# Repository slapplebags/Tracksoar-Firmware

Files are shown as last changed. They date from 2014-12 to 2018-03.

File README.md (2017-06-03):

## Tracksoar Firmware
==========
This is a modified version of the [trackduino](https://github.com/trackuino/trackuino) firmware for the [Tracksoar](www.tracksoar.com) hardware.

### Configuring Hardware Version
This branch uses a super basic HAL and as a result must be told what version of hardware it is running on. [Edit the config here](https://github.com/slapplebags/Tracksoar-Firmware/blob/BME280-support/Tracksoar/Firmware/tracksoar/config.h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) to have the corect version uncommented. Everything before V1.2 should work as it normally did on the old set of sensors.

#### Build Status


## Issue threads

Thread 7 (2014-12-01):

Solar Version

slapplebags, 2014-12-01:
Create a solar version without 3.3 / 5v regs. Need to added a transistor to power up / down the radiometrix module and a buckboost to supply the 5v. Need to add a solar charger for lipo and see if the trackuino software will run at 4 or 8 mhz.

slapplebags, 2015-01-05:
By replacing the existing 5v regulator this could work with the existing design.

slapplebags, 2015-04-12:
Created solar version of the board.

Closed 2015-04-12.

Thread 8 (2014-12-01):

Update atmega328

slapplebags, 2014-12-01:
look into updating the atmega 328p to an atmega32u4 or similar for direct usb programability. This may shed some weight / size in connectors.

slapplebags, 2015-01-05:
Existing code allows for a atmega32u4, will looking into updating this on future revisions.

slapplebags, 2015-04-12:
Any future versions will be ARM based. Switching to the 32u4 is not worth the time to re-lay out the board . In addition a USB micro connector would not save space over the current FTDI connector.

Closed 2015-04-12.

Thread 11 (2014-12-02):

research new gps module

slapplebags, 2014-12-02:
look into the ublox uc530, it will fit on the existing board and integrates a chip antenna to reduce part count.

slapplebags, 2015-01-05:
Found the issue with the existing ublox max 7, need to provide power to the active antenna. However including the uc530 will reduce part count and weight by eliminating the u.fl connector and external active antenna. This will likely be included on the next revision.

slapplebags, 2015-04-12:
replaced max 7 with current gen max 8 / gps chip antenna and resolved issues with NMEA sentences. No need to move to the uc530.

Closed 2015-04-12.

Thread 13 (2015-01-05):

FTDI timeout

slapplebags, 2015-01-05:
When programming the board via FTDI the operation times out with no response. Seems to be related to the pull up / cap on the reset line.

slapplebags, 2015-01-05:
Reset cap was wired incorrectly on the board. Fixed by moving where cap is in the circuit. New boards have been ordered.

Closed 2015-01-05.

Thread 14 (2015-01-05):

Smaller GPS antenna

slapplebags, 2015-01-05:
Replace the existing GPS patch antenna with a smaller (fits within board outline) model. the following is a good candidate: http://www.taoglas.com/images/product_images/original_images/AP.10E.07.0039B.pdf

slapplebags, 2015-04-12:
Replaced with the above listed antenna, works well.

Closed 2015-04-12.

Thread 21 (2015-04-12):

No Sensor Data

slapplebags, 2015-04-12:
the current firmware does not include code for the BMP180 / SHT21 sensors.

slapplebags, 2015-04-27:
Latest commit to testing branch works! will make that the only firmware file shortly.

Closed 2015-04-27.

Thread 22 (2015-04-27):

Replace serial headers with MUX(S)

slapplebags, 2015-04-27:
Replace the painful and manual serial headers / jumpers with a mux to automatically select between programming and flight modes.

slapplebags, 2015-04-27:
reviewing using a pair of these muxes: http://www.ti.com/lit/ds/symlink/sn74lvc1g3157.pdf

slapplebags, 2015-05-18:
board has been created and ordered.

slapplebags, 2015-06-10:
test board arrived

slapplebags, 2015-07-31:
shelved for now, its a whole thing.

Closed 2015-07-31.

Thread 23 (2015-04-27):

Power Usage

slapplebags, 2015-04-27:
implement software power optimization. Batteries currently only 12 hours at room temp or last 3 hours at -40c.

mkapuscik, 2019-02-27:
So what in particular do you want optimized. Are there specific loops that are blocking that waste power? Sensors that stay on that shouldn't? Unnecessary delay calls?

It's incredibly helpful to characterize a problem before making an issue about it because it's much easier to tackle a specific set of symptoms that can be veritably solved than to "make it better" which could have no definite end and has infinite scope.

slapplebags, 2019-02-27:
Issue has been resolved, battery life extended to 36 hours at room temp and 12 hours at -40c.

Closed 2019-02-27.

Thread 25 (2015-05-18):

License

slapplebags, 2015-05-18:
update licenses to non-commercial until the board is ready for sale.

mkapuscik, 2016-09-05:
This is already the case for the hardware

Closed 2016-09-05.

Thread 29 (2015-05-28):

Integrate RF PA onto Tracksoar board.

mkapuscik, 2015-05-28:
Implement discrete component or monolithic RF PA onto Tracksoar PCB for 144MHz.

mkapuscik, 2015-05-28:
TI's CC11xx series monolithic transceivers have options that support 2-FSK modulation and the [CC1120](http://www.ti.com/lit/ds/symlink/cc1120.pdf) "supports" down to 136.7MHz however is not characterized below 169 MHz.

slapplebags, 2015-05-28:
what about the MAX2606, small package, low external part count, etc.

slapplebags, 2015-06-10:
also an ADL5545 to up the transmit power to 250mw

slapplebags, 2015-07-31:
Mike found a promising new chip, beat the info out of him so we can look into it.

slapplebags, 2015-09-14:
here's an example max2606: http://ram.lijun.li/old/various/fm_xmtr.html

slapplebags, 2016-02-01:
another possiblitity: http://digitalcommons.calpoly.edu/cgi/viewcontent.cgi?article=1156&context=eesp
also max2470 is a whole thing, use the micrl300

mkapuscik, 2019-02-27:
Wrong repo for this

Closed 2019-02-27.

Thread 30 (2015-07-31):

Sensor Calibration

slapplebags, 2015-07-31:
Running the tracksoar on the ground in stable conditions I get fairly poor data from the sensors, negative pressures at sea level, humidity off by 10%, and temp is questionable.

slapplebags, 2019-02-27:
BME280 sensor has resolved these issues.

Closed 2019-02-27.

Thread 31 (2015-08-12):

Potential Sensor Replacement

slapplebags, 2015-08-12:
replace the 2 sensors currently handling temperature / pressure / humidity with one sensor to handle all three such as:
http://www.mouser.com/ProductDetail/Bosch-Sensortec/BME280/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

mkapuscik, 2016-09-04:
See 5e0e7ec and let me know how testing works.

mkapuscik, 2016-09-05:
Test #39 with 1.2 and <1.2 boards and this can be resolved.

mkapuscik, 2019-02-27:
@slapplebags can you verify this is working. Can I close this?

slapplebags, 2019-02-27:
sensors have been replaced with the BME280 in tracksoar v1.2 and v2. Issue is resolved.

Closed 2019-02-27.

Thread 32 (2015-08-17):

GPS lost over 66426ft

slapplebags, 2015-08-17:
It looks like the GPS flight mode config at boot is happening correctly. May check the following: http://forum.arduino.cc/index.php?topic=232896.0
to resolve the issue and verify the config is happening.

slapplebags, 2015-09-10:
Verified that the GPS is being properly put into flight mode, the issue is the GPS antenna was getting too cold which detuned the antenna.

Closed 2015-09-10.

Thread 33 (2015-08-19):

add battery backup

slapplebags, 2015-08-19:
a battery like this would do nicely:
http://www.sii.co.jp/en/me/files/2014/11/BAC3011EJ-01C1409_web__.pdf

slapplebags, 2015-08-19:
added new board revision with a battery backup on board. Will send out for a new board revision soon.

Closed 2015-09-10.

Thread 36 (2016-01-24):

SD Card SRAM usage

slapplebags, 2016-01-24:
Look at switching to an eeprom like the ST Micro M24M02 to resolve issues with SD card library SRAM usage.

appropriate library for the ST Micro M24M02:
https://github.com/JChristensen/extEEPROM/blob/master/extEEPROM.cpp

slapplebags, 2019-02-27:
ATMega32u4 has enough SRAM to handle SD card / FAT libraries to enable onboard datalogging.

Closed 2019-02-27.

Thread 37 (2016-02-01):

Update Trackuino.ino to latest Arduino IDE

slapplebags, 2016-02-01:
The Trackuino.ide no longer compiles under 1.6.6+ due to a change in prog_uchar

slapplebags, 2016-02-01:
this may have point to a fix: http://arduino.stackexchange.com/questions/13816/updating-max7456-library-to-work-with-arduino-1-6-6

fake-name, 2018-03-24:
Works in current platformio.

slapplebags, 2019-02-27:
Issue is resolved. Tracksoar works with modern arduino versions.

Closed 2019-02-27.

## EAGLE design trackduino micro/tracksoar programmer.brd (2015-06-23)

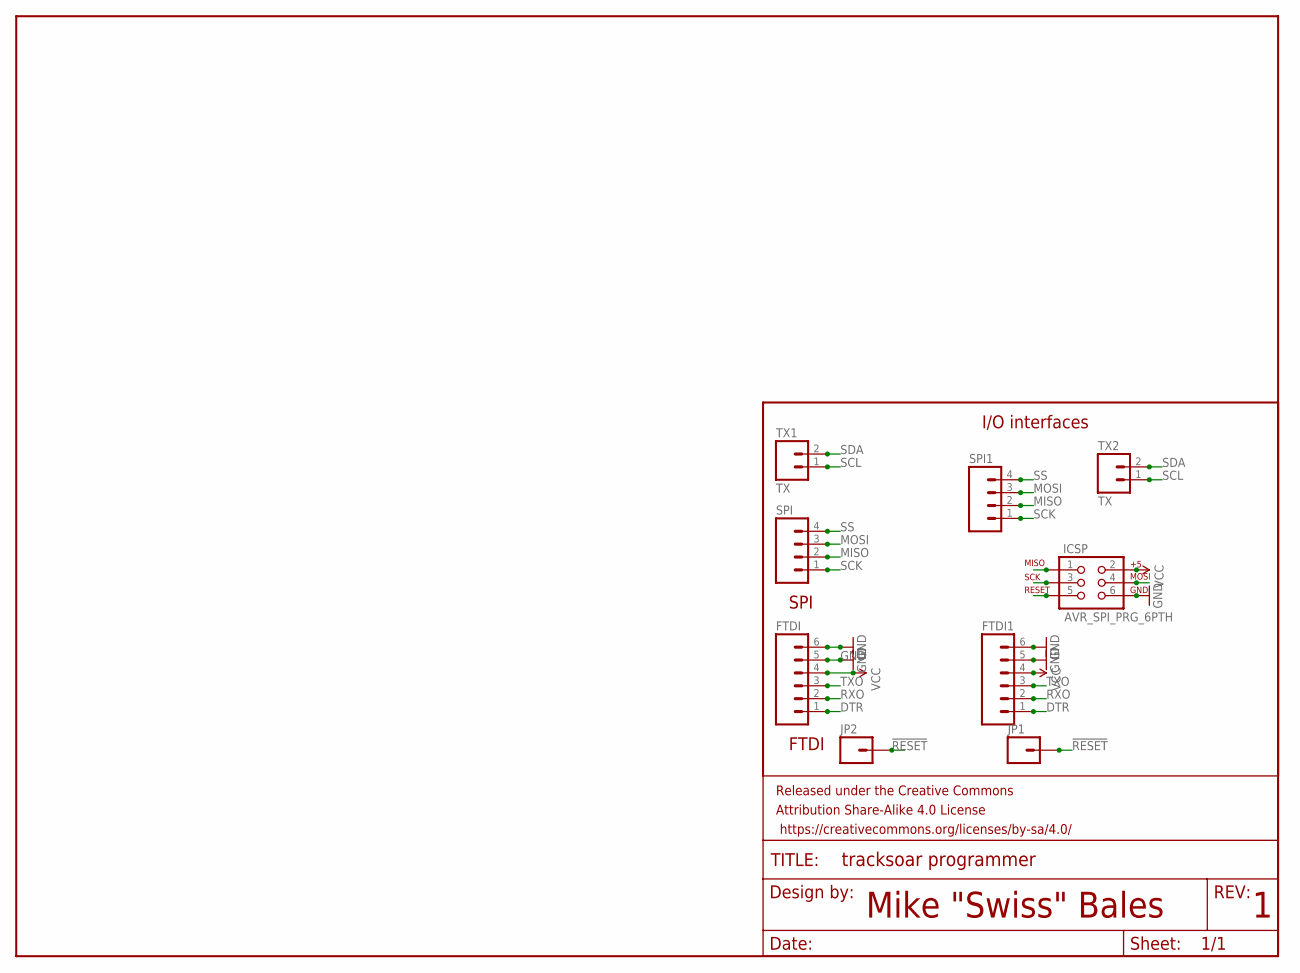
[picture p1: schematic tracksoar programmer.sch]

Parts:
FRAME1: FRAME-LETTER; CREATIVE_COMMONS
FTDI, FTDI1: M06NO_SILK_FEMALE_PTH; 1X06_NO_SILK
ICSP: AVR_SPI_PRG_6PTH; 2X3
JP1, JP2: M01PTH; 1X01
SPI, SPI1: M04JST-PTH-VERT; JST-4-PTH-VERT
TX1, TX2: TX; JST-2-PTH-VERT

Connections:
!RESET: ICSP.5, JP1.1, JP2.1
DTR: FTDI.1, FTDI1.1
GND: FTDI.5, FTDI.6, FTDI1.5, FTDI1.6, ICSP.6
MISO: ICSP.1, SPI.2, SPI1.2
MOSI: ICSP.4, SPI.3, SPI1.3
RXO: FTDI.2, FTDI1.2
SCK: ICSP.3, SPI.1, SPI1.1
SCL: TX1.1, TX2.1
SDA: TX1.2, TX2.2
SS: SPI.4, SPI1.4
TXO: FTDI.3, FTDI1.3
VCC: FTDI.4, FTDI1.4, ICSP.2

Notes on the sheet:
Mike "Swiss" Bales
I/O interfaces
SPI
FTDI

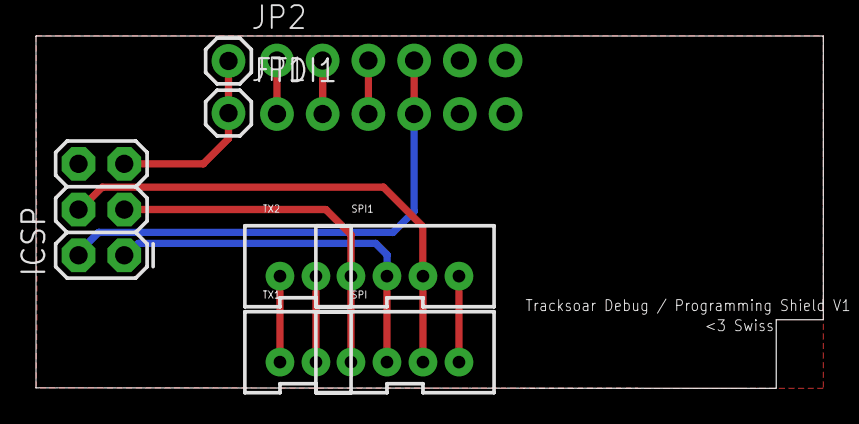
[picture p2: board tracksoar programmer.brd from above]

Board: 2 copper layers, 43.7 x 19.6 mm, 10 parts (1 on the bottom side), 12 nets.

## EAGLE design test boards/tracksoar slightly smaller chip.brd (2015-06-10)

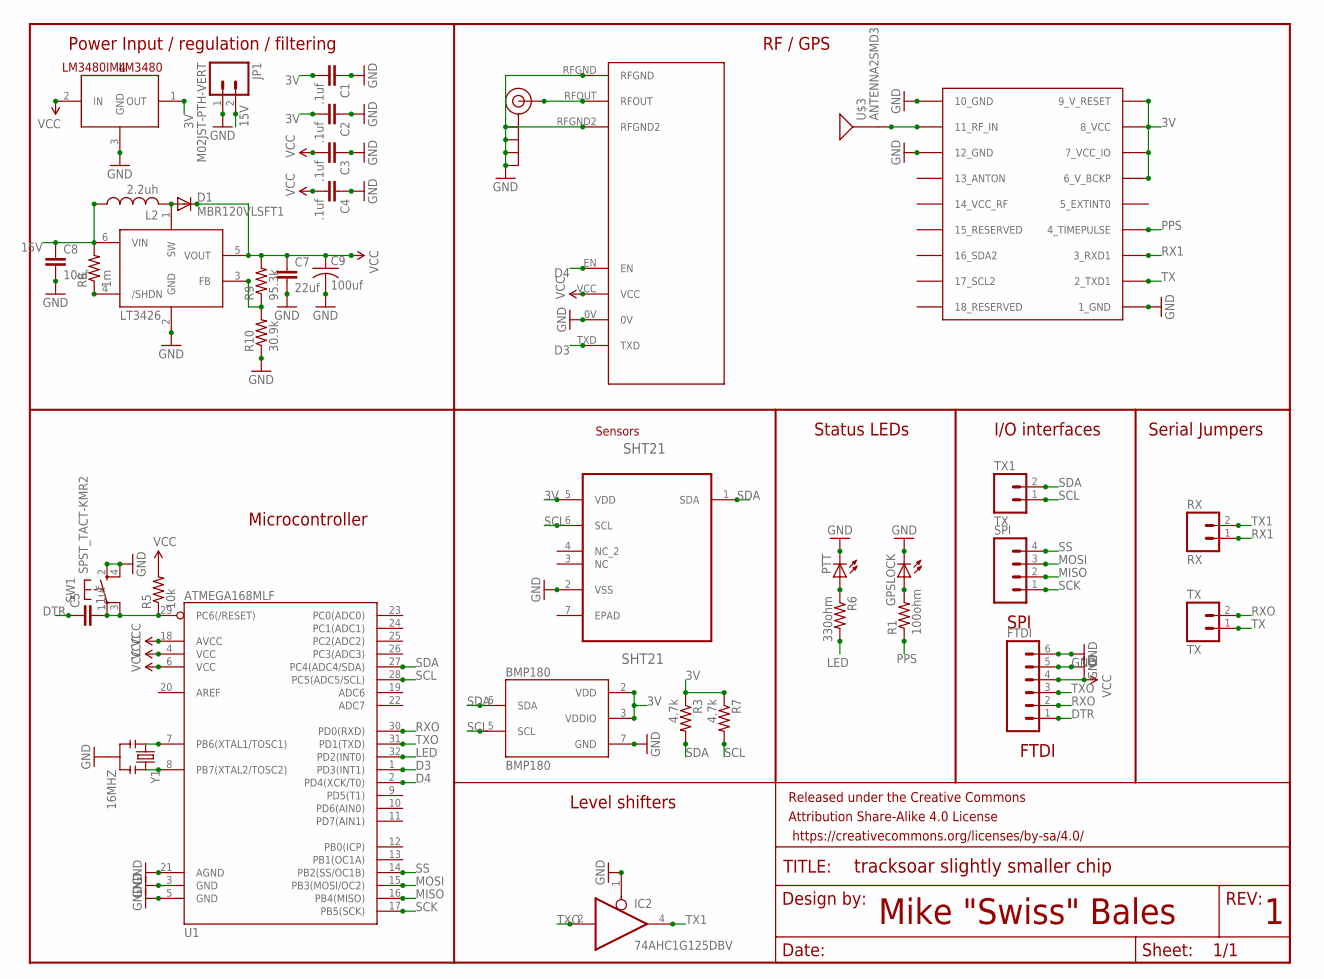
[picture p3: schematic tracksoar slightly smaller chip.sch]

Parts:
BMP180: BMP180
C1, C2, C3, C4, C5: .1uf; 0805
C7: 22uf; 0805
C8: 10uf; 0805
C9: 100uf; C1206
D1: MBR120VLSFT1; SOD123
FRAME1: FRAME-LETTER; CREATIVE_COMMONS
FTDI: M06NO_SILK_FEMALE_PTH; 1X06_NO_SILK
GPSLOCK: LEDCHIP-LED0805; CHIP-LED0805
IC2: 74AHC1G125DBV; SOT23-5
J$1: SMA_EDGE; SMA-EDGE
JP1: M02JST-PTH-VERT; JST-2-PTH-VERT
L2: 2.2uh; L1812
LM3480: LM3480IM4; SOT23-3
LT3426: LT3426; SOT23-6
PTT: LEDCHIP-LED0805; CHIP-LED0805
R1: 100ohm; 0805
R3, R7: 4.7k; 0805
R5: 10k; 0805
R6: 330ohm; 0805
R8: 1m; 0805
R9: 95.3k; 0805
R10: 30.9k; 0805
RX: RX; JST-2-PTH-VERT
SHT21: SHT21; DFN300X300X110-7N
SPI: M04JST-PTH-VERT; JST-4-PTH-VERT
SW1: SPST_TACT-KMR2; KMR2
TX, TX1: TX; JST-2-PTH-VERT
U1: ATMEGA168MLF; MLF32
U$1: UBLOX_MAX
U$2: RADIOMETRIX-HX1
U$3: ANTENNA2SMD3; ANTENNA-CHIP4
Y1: 16MHZ; RESONATOR-SMD

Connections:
3V: BMP180.2 (VDD), BMP180.3 (VDDIO), C1.2, C2.2, LM3480.1 (OUT), R3.1, R7.1, SHT21.5 (VDD), U$1.6_V_BCKP, U$1.7_VCC_IO, U$1.8_VCC, U$1.9_V_RESET
15V: C8.1, JP1.2, L2.1, LT3426.6 (VIN), R8.2
D3: U1.1 (PD3(INT1)), U$2.TXD
D4: U1.2 (PD4(XCK/T0)), U$2.EN
DTR: C5.1, FTDI.1
GND: BMP180.7 (GND), C1.1, C2.1, C3.1, C4.1, C7.2, C8.2, C9.2, FTDI.5, FTDI.6, GPSLOCK.C, IC2.1 (OE), IC2.3 (GND), J$1.GND@0 (GND), J$1.GND@1 (GND), J$1.GND@2 (GND), J$1.GND@3 (GND), JP1.1, LM3480.3 (GND), LT3426.2 (GND), PTT.C, R10.1, SHT21.2 (VSS), SW1.2 (S), SW1.4 (S1), U1.3 (GND), U1.5 (GND), U1.21 (AGND), U$1.1_GND, U$1.10_GND, U$1.12_GND, U$2.0V, U$2.RFGND, U$2.RFGND2, Y1.2
LED: R6.2, U1.32 (PD2(INT0))
MISO: SPI.2, U1.16 (PB4(MISO))
MOSI: SPI.3, U1.15 (PB3(MOSI/OC2))
unnamed: J$1.SIG (SIGNAL), U$2.RFOUT
unnamed: GPSLOCK.A, R1.2
unnamed: U$1.11_RF_IN, U$3.SIG
unnamed: D1.A, L2.2, LT3426.1 (SW)
unnamed: LT3426.4 (/SHDN), R8.1
unnamed: LT3426.3 (FB), R9.1, R10.2
unnamed: U1.8 (PB7(XTAL2/TOSC2)), Y1.3
unnamed: C5.2, R5.1, SW1.1, SW1.3 (P1), U1.29 (PC6(/RESET))
unnamed: U1.7 (PB6(XTAL1/TOSC1)), Y1.1
unnamed: PTT.A, R6.1
PPS: R1.1, U$1.4_TIMEPULSE
RX1: RX.1, U$1.3_RXD1
RXO: FTDI.2, TX.2, U1.30 (PD0(RXD))
SCK: SPI.1, U1.17 (PB5(SCK))
SCL: BMP180.5 (SCL), R7.2, SHT21.6 (SCL), TX1.1, U1.28 (PC5(ADC5/SCL))
SDA: BMP180.6 (SDA), R3.2, SHT21.1 (SDA), TX1.2, U1.27 (PC4(ADC4/SDA))
SS: SPI.4, U1.14 (PB2(SS/OC1B))
TX: TX.1, U$1.2_TXD1
TX1: IC2.4 (O), RX.2
TXO: FTDI.3, IC2.2 (I), U1.31 (PD1(TXD))
VCC: C3.2, C4.2, C7.1, C9.1, D1.C, FTDI.4, IC2.5 (VCC), LM3480.2 (IN), LT3426.5 (VOUT), R5.2, R9.2, U1.4 (VCC), U1.6 (VCC), U1.18 (AVCC), U$2.VCC

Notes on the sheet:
Mike "Swiss" Bales
Power Input / regulation / filtering
RF / GPS
Microcontroller
Level shifters
Status LEDs
I/O interfaces
Serial Jumpers
SPI
FTDI
Sensors

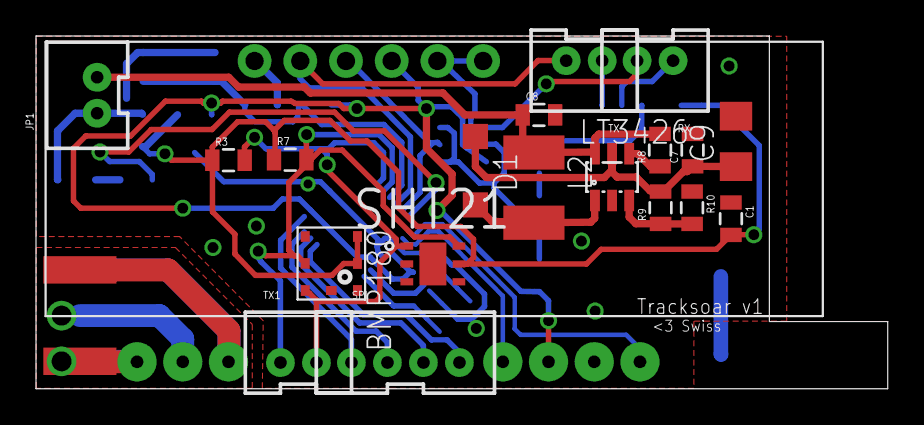
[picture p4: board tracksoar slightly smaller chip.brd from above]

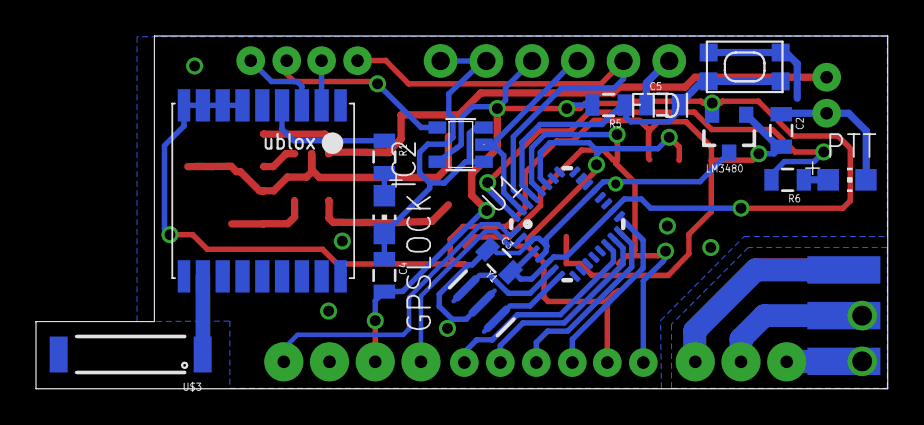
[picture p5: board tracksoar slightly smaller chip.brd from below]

Board: 2 copper layers, 47.3 x 19.6 mm, 39 parts (18 on the bottom side), 30 nets.

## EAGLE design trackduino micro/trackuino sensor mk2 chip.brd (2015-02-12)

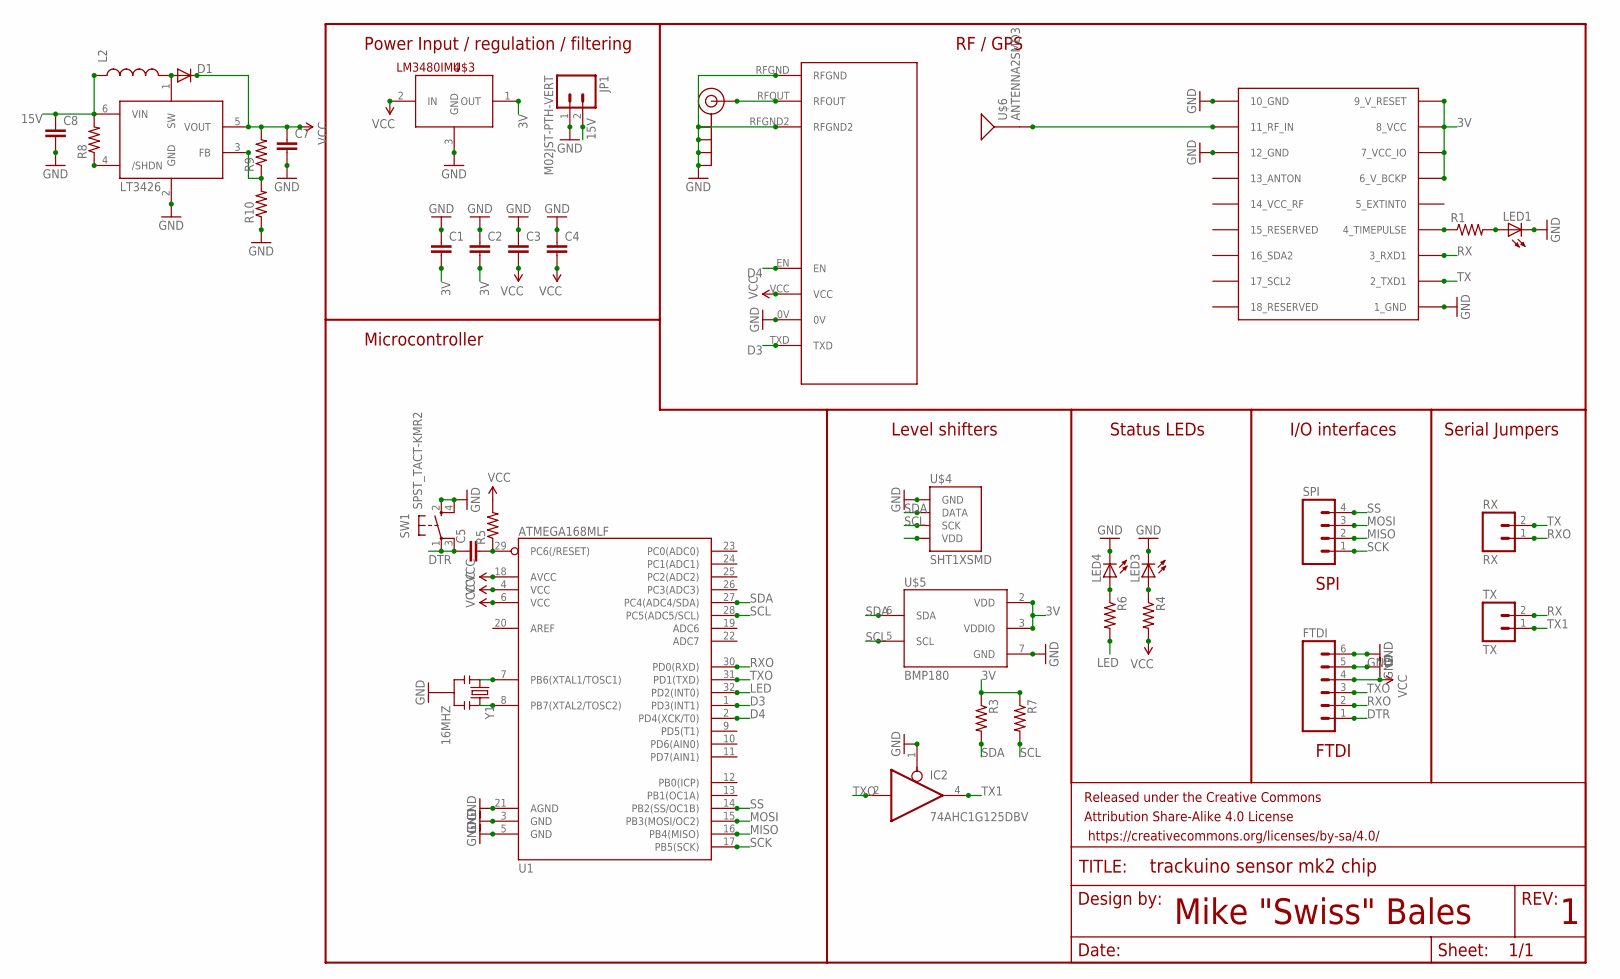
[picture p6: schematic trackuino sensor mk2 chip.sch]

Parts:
C1, C2, C3, C4, C5, C7, C8: CAP0805; 0805
D1: DIODE-SOD123; SOD123
FRAME1: FRAME-LETTER; CREATIVE_COMMONS
FTDI: M06NO_SILK_FEMALE_PTH; 1X06_NO_SILK
IC2: 74AHC1G125DBV; SOT23-5
J$1: SMA_EDGE; SMA-EDGE
JP1: M02JST-PTH-VERT; JST-2-PTH-VERT
L2: INDUCTOR0805; 0805
LED1, LED3, LED4: LEDCHIP-LED0805; CHIP-LED0805
R1, R3, R4, R5, R6, R7, R8, R9, R10: RESISTOR0805-RES; 0805
RX: RX; 1X02
SPI: M041X04_NO_SILK; 1X04_NO_SILK
SW1: SPST_TACT-KMR2; KMR2
TX: TX; 1X02
U1: ATMEGA168MLF; MLF32
U$1: UBLOX_MAX
U$2: RADIOMETRIX-HX1
U$3: LM3480IM4; SOT23-3
U$4: SHT1XSMD; SHT1X
U$5: BMP180
U$6: ANTENNA2SMD3; ANTENNA-CHIP4
U$7: LT3426; SOT23-6
Y1: 16MHZ; RESONATOR-SMD

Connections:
3V: C1.2, C2.2, R3.1, R7.1, U$1.6_V_BCKP, U$1.7_VCC_IO, U$1.8_VCC, U$1.9_V_RESET, U$3.1 (OUT), U$4.4 (VDD), U$5.2 (VDD), U$5.3 (VDDIO)
15V: C8.1, JP1.2, L2.1, R8.2, U$7.6 (VIN)
D3: U1.1 (PD3(INT1)), U$2.TXD
D4: U1.2 (PD4(XCK/T0)), U$2.EN
DTR: C5.1, FTDI.1, SW1.1, SW1.3 (P1)
GND: C1.1, C2.1, C3.1, C4.1, C7.2, C8.2, FTDI.5, FTDI.6, IC2.1 (OE), IC2.3 (GND), J$1.GND@0 (GND), J$1.GND@1 (GND), J$1.GND@2 (GND), J$1.GND@3 (GND), JP1.1, LED1.C, LED3.C, LED4.C, R10.1, SW1.2 (S), SW1.4 (S1), U1.3 (GND), U1.5 (GND), U1.21 (AGND), U$1.1_GND, U$1.10_GND, U$1.12_GND, U$2.0V, U$2.RFGND, U$2.RFGND2, U$3.3 (GND), U$4.1 (GND), U$5.7 (GND), U$7.2 (GND), Y1.2
LED: R6.2, U1.32 (PD2(INT0))
MISO: SPI.2, U1.16 (PB4(MISO))
MOSI: SPI.3, U1.15 (PB3(MOSI/OC2))
unnamed: J$1.SIG (SIGNAL), U$2.RFOUT
unnamed: R1.1, U$1.4_TIMEPULSE
unnamed: LED1.A, R1.2
unnamed: U$1.11_RF_IN, U$6.SIG
unnamed: C5.2, R5.1, U1.29 (PC6(/RESET))
unnamed: LED3.A, R4.1
unnamed: D1.A, L2.2, U$7.1 (SW)
unnamed: R8.1, U$7.4 (/SHDN)
unnamed: R9.1, R10.2, U$7.3 (FB)
unnamed: U1.8 (PB7(XTAL2/TOSC2)), Y1.3
unnamed: U1.7 (PB6(XTAL1/TOSC1)), Y1.1
unnamed: LED4.A, R6.1
RX: TX.2, U$1.3_RXD1
RXO: FTDI.2, RX.1, U1.30 (PD0(RXD))
SCK: SPI.1, U1.17 (PB5(SCK))
SCL: R7.2, U1.28 (PC5(ADC5/SCL)), U$4.3 (SCK), U$5.5 (SCL)
SDA: R3.2, U1.27 (PC4(ADC4/SDA)), U$4.2 (DATA), U$5.6 (SDA)
SS: SPI.4, U1.14 (PB2(SS/OC1B))
TX: RX.2, U$1.2_TXD1
TX1: IC2.4 (O), TX.1
TXO: FTDI.3, IC2.2 (I), U1.31 (PD1(TXD))
VCC: C3.2, C4.2, C7.1, D1.C, FTDI.4, IC2.5 (VCC), R4.2, R5.2, R9.2, U1.4 (VCC), U1.6 (VCC), U1.18 (AVCC), U$2.VCC, U$3.2 (IN), U$7.5 (VOUT)

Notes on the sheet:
Mike "Swiss" Bales
Power Input / regulation / filtering
RF / GPS
Microcontroller
Level shifters
Status LEDs
I/O interfaces
Serial Jumpers
SPI
FTDI

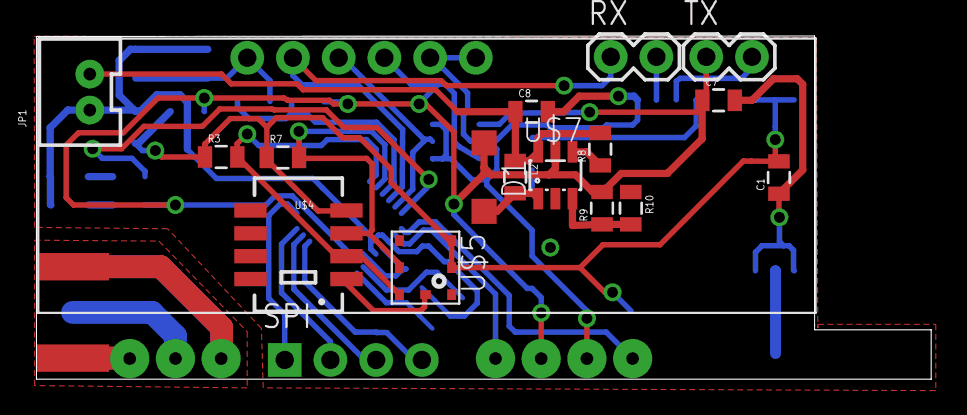
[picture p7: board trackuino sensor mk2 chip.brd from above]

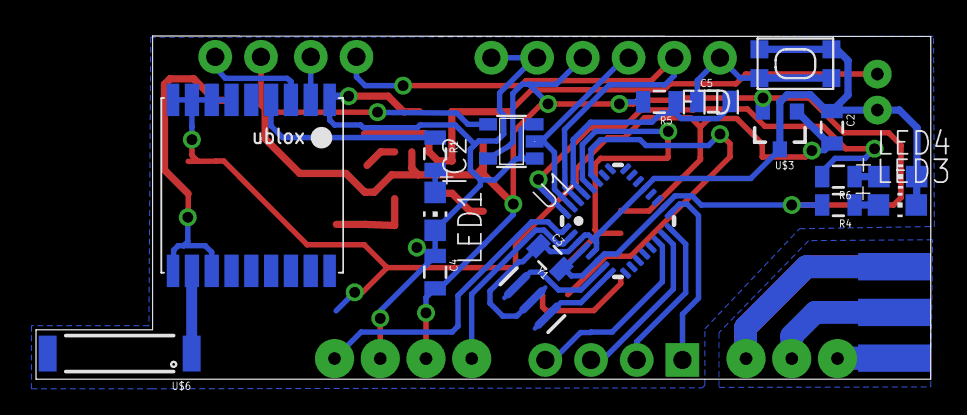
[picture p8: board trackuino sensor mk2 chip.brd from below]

Board: 2 copper layers, 49.7 x 19.1 mm, 39 parts (20 on the bottom side), 31 nets.

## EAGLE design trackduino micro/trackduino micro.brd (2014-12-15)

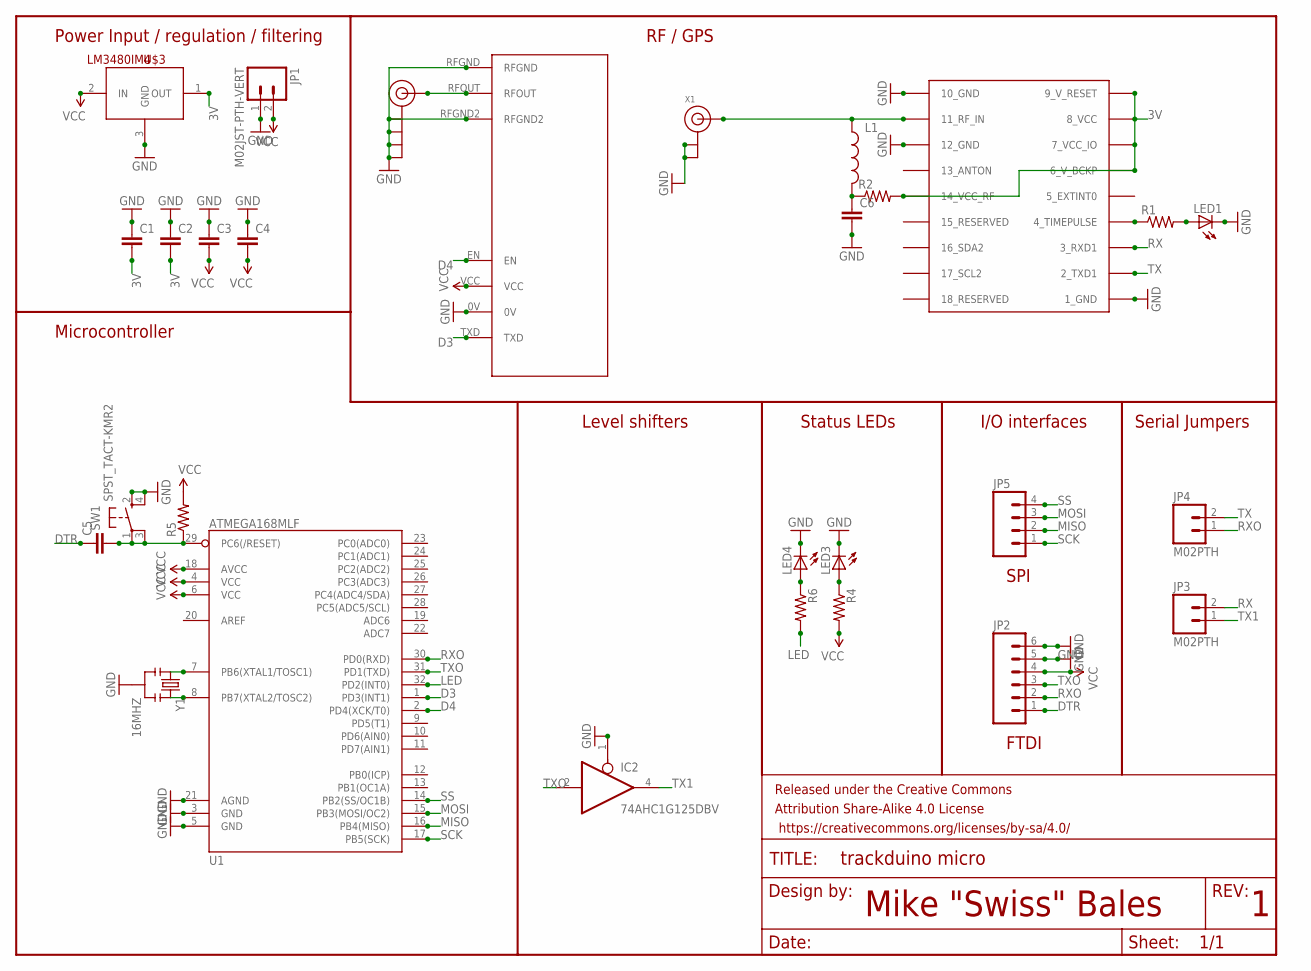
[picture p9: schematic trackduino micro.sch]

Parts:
C1, C2, C3, C4, C5, C6: CAP0805; 0805
FRAME1: FRAME-LETTER; CREATIVE_COMMONS
IC2: 74AHC1G125DBV; SOT23-5
J$1: SMA_EDGE; SMA-EDGE
JP1: M02JST-PTH-VERT; JST-2-PTH-VERT
JP2: M06NO_SILK_FEMALE_PTH; 1X06_NO_SILK
JP3, JP4: M02PTH; 1X02
JP5: M041X04_NO_SILK; 1X04_NO_SILK
L1: INDUCTOR0805; 0805
LED1, LED3, LED4: LEDCHIP-LED0805; CHIP-LED0805
R1, R2, R4, R5, R6: RESISTOR0805-RES; 0805
SW1: SPST_TACT-KMR2; KMR2
U1: ATMEGA168MLF; MLF32
U$1: UBLOX_MAX
U$2: RADIOMETRIX-HX1
U$3: LM3480IM4; SOT23-3
X1: ANTENNA_U.FL; U.FL
Y1: 16MHZ; RESONATOR-SMD

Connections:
3V: C1.2, C2.2, R2.2, U$1.6_V_BCKP, U$1.7_VCC_IO, U$1.8_VCC, U$1.9_V_RESET, U$1.14_VCC_RF, U$3.1 (OUT)
D3: U1.1 (PD3(INT1)), U$2.TXD
D4: U1.2 (PD4(XCK/T0)), U$2.EN
DTR: C5.1, JP2.1
GND: C1.1, C2.1, C3.1, C4.1, C6.2, IC2.1 (OE), IC2.3 (GND), J$1.GND@0 (GND), J$1.GND@1 (GND), J$1.GND@2 (GND), J$1.GND@3 (GND), JP1.1, JP2.5, JP2.6, LED1.C, LED3.C, LED4.C, SW1.2 (S), SW1.4 (S1), U1.3 (GND), U1.5 (GND), U1.21 (AGND), U$1.1_GND, U$1.10_GND, U$1.12_GND, U$2.0V, U$2.RFGND, U$2.RFGND2, U$3.3 (GND), X1.1 (GND), X1.2 (GND), Y1.2
LED: R6.2, U1.32 (PD2(INT0))
MISO: JP5.2, U1.16 (PB4(MISO))
MOSI: JP5.3, U1.15 (PB3(MOSI/OC2))
unnamed: J$1.SIG (SIGNAL), U$2.RFOUT
unnamed: R1.1, U$1.4_TIMEPULSE
unnamed: LED1.A, R1.2
unnamed: L1.1, U$1.11_RF_IN, X1.3 (SIGNAL)
unnamed: LED3.A, R4.1
unnamed: C5.2, R5.1, SW1.1, SW1.3 (P1), U1.29 (PC6(/RESET))
unnamed: U1.8 (PB7(XTAL2/TOSC2)), Y1.3
unnamed: C6.1, L1.2, R2.1
unnamed: U1.7 (PB6(XTAL1/TOSC1)), Y1.1
unnamed: LED4.A, R6.1
RX: JP3.2, U$1.3_RXD1
RXO: JP2.2, JP4.1, U1.30 (PD0(RXD))
SCK: JP5.1, U1.17 (PB5(SCK))
SS: JP5.4, U1.14 (PB2(SS/OC1B))
TX: JP4.2, U$1.2_TXD1
TX1: IC2.4 (O), JP3.1
TXO: IC2.2 (I), JP2.3, U1.31 (PD1(TXD))
VCC: C3.2, C4.2, IC2.5 (VCC), JP1.2, JP2.4, R4.2, R5.2, U1.4 (VCC), U1.6 (VCC), U1.18 (AVCC), U$2.VCC, U$3.2 (IN)

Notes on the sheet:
Mike "Swiss" Bales
Power Input / regulation / filtering
RF / GPS
Microcontroller
Level shifters
Status LEDs
I/O interfaces
Serial Jumpers
SPI
FTDI

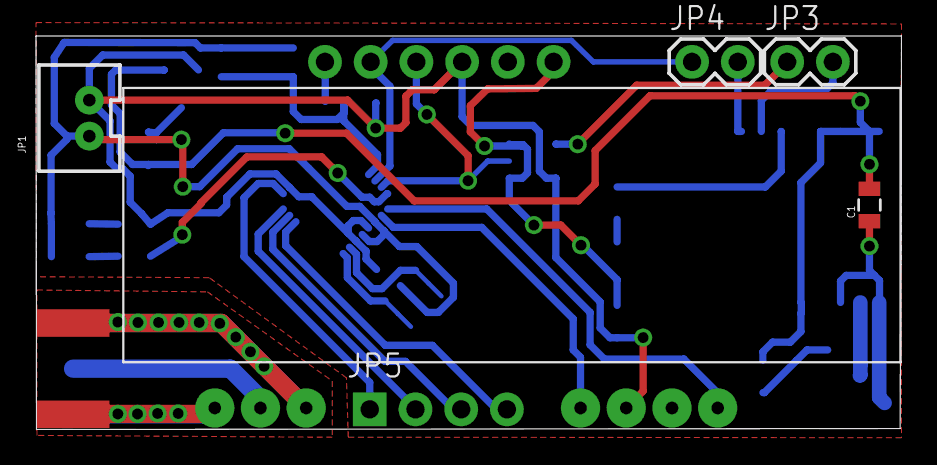
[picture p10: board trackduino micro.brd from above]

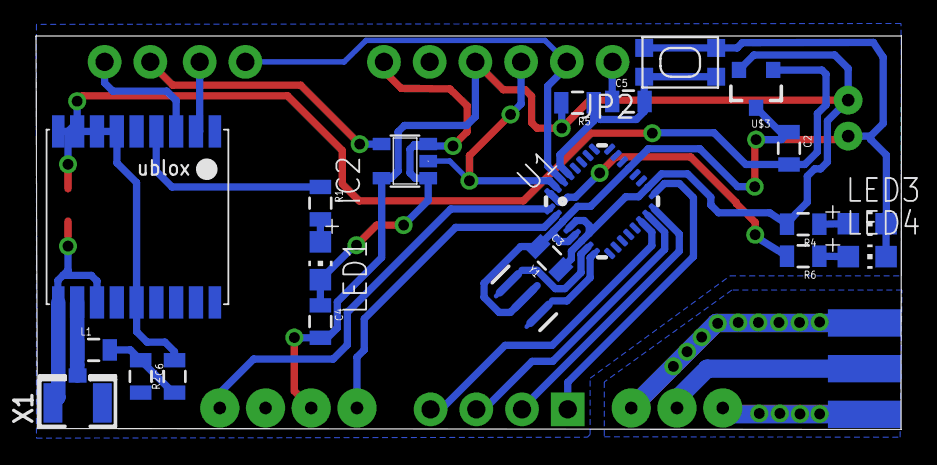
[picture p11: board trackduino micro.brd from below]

Board: 2 copper layers, 48.1 x 21.9 mm, 30 parts (23 on the bottom side), 26 nets.

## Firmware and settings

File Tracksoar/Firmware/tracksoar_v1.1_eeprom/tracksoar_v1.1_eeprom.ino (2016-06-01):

/* trackuino copyright (C) 2010  EA5HAV Javi
 *
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
 * You should have received a copy of the GNU General Public License
 * along with this program; if not, write to the Free Software
 * Foundation, Inc., 51 Franklin Street, Fifth Floor, Boston, MA  02110-1301, USA.
 */

// Mpide 22 fails to compile Arduino code because it stupidly defines ARDUINO 
// as an empty macro (hence the +0 hack). UNO32 builds are fine. Just use the
// real Arduino IDE for Arduino builds. Optionally complain to the Mpide
// authors to fix the broken macro.
#if (ARDUINO + 0) == 0
#error "Oops! We need the real Arduino IDE (version 22 or 23) for Arduino builds."
#error "See trackuino.pde for details on this"

// Refuse to compile on arduino version 21 or lower. 22 includes an
// optimization of the USART code that is critical for real-time operation
// of the AVR code.
#elif (ARDUINO + 0) < 22
#error "Oops! We need Arduino 22 or 23"
#error "See trackuino.pde for details on this"

#endif


// Trackuino custom libs
#include "config.h"
#include "afsk_avr.h"
//#include "afsk_pic32.h"
#include "aprs.h"
//#include "buzzer.h"
#include "gps.h"
#include "pin.h"
#include "power.h"
#include "sensors_avr.h"
//#include "sensors_pic32.h"
//#include <SPI.h>
//#include <SD.h>

// Arduino/AVR libs
#if (ARDUINO + 1) >= 100
#  include <Arduino.h>
#else
#  include <WProgram.h>
#endif
#define cbi(sfr, bit) (_SFR_BYTE(sfr) &= ~_BV(bit))
// Module constants
static const uint32_t VALID_POS_TIMEOUT = 2000;  // ms

// Though not used here, we need to include Wire.h in this file for other code:
#include <Wire.h>

#include "extEEPROM.h"

// Module variables
static int32_t next_aprs = 0;
uint32_t g_last_data_write_time = 0;
extEEPROM g_EEPROM(kbits_2048, 1, 256);

void setup()
{
  pinMode(LED_PIN, OUTPUT);
  pin_write(LED_PIN, LOW);

// deactivate internal pull-ups for twi
    // as per note from atmega8 manual pg167
    cbi(PORTC, 4);
    cbi(PORTC, 5);

  Serial.begin(GPS_BAUDRATE);
#ifdef DEBUG_RESET
  Serial.println("RESET");
#endif

//  buzzer_setup();
  afsk_setup();
  gps_setup();
  sensors_setup();

#ifdef DEBUG_SENS
  Serial.print("Ti=");
  Serial.print(sensors_int_lm60());
  Serial.print(", Te=");
  Serial.print(sensors_ext_lm60());
  Serial.print(", Vin=");
  Serial.println(sensors_vin());
#endif

  // Do not start until we get a valid time reference
  // for slotted transmissions.
  if (APRS_SLOT >= 0) {
    do {
      while (! Serial.available())
        power_save();
    } while (! gps_decode(Serial.read()));
    
    next_aprs = millis() + 1000 *
      (APRS_PERIOD - (gps_seconds + APRS_PERIOD - APRS_SLOT) % APRS_PERIOD);
  }
  else {
    next_aprs = millis();
  }  
  // TODO: beep while we get a fix, maybe indicating the number of
  // visible satellites by a series of short beeps?
}

void get_pos()
{
  // Get a valid position from the GPS
  int valid_pos = 0;
  uint32_t timeout = millis();
  do {
    if (Serial.available())
      valid_pos = gps_decode(Serial.read());
  } while ( (millis() - timeout < VALID_POS_TIMEOUT) && ! valid_pos) ;

}

void writeData()
{
  g_EEPROM.writeData(gps_time);
  g_EEPROM.writeData(gps_seconds);
  g_EEPROM.writeData(gps_lat);
  g_EEPROM.writeData(gps_lon);
  g_EEPROM.writeData(gps_altitude);
  float temperature = sensors_temperature();
  g_EEPROM.writeData(temperature);
  int32_t pressure = sensors_pressure();
  g_EEPROM.writeData(pressure);
  float humidity = sensors_humidity();
  g_EEPROM.writeData(humidity);
  g_last_data_write_time = millis();
}

void loop()
{
  // Time for another APRS frame
  if ((int32_t) (millis() - next_aprs) >= 0) {
    get_pos();
    aprs_send();
    next_aprs += APRS_PERIOD * 1000L;
    while (afsk_flush()) {
      power_save();
    }

  if ((millis() - g_last_data_write_time) >= SD_WRITE_INTERVAL)
  {
    writeData();
  }

#ifdef DEBUG_MODEM
    // Show modem ISR stats from the previous transmission
    afsk_debug();
#endif
  }

  power_save(); // Incoming GPS data or interrupts will wake us up
}

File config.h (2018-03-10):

/* trackuino copyright (C) 2010  EA5HAV Javi

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
   You should have received a copy of the GNU General Public License
   along with this program; if not, write to the Free Software Foundation,
   Inc., 51 Franklin Street, Fifth Floor, Boston, MA  02110-1301, USA.
*/

#ifndef __CONFIG_H__
#define __CONFIG_H__

// ---------------------------------------------------------------------------------
// THIS IS THE TRACKSOAR FIRMWARE CONFIGURATION FILE
// WHERE YOU ENTER YOUR CALLSIGN AND OTHER SETTINGS.
//
// NOTE: all pins are Arduino based, not the Atmega chip.
// Mapping: http://www.arduino.cc/en/Hacking/PinMapping
// ---------------------------------------------------------------------------------


// Set your CALLSIGN and SSID. The SSID for a Balloon is 11.
// For other common SSID values see http://zlhams.wikidot.com/aprs-ssidguide
#define S_CALLSIGN      "VE6ATV"
#define S_CALLSIGN_ID   11
// *************************************************


// Set DESTINATION CALLSIGN.
// The following (default), APRS (with SSID=0), is usually okay.
#define D_CALLSIGN      "APRS"
#define D_CALLSIGN_ID   0
// *************************************************


// DIGIPEATING PATH(s).
// (read more about digipeating paths here: http://wa8lmf.net/DigiPaths/ )
// ---------------------------------------------------------------------------------
// The recommended digi path for a balloon is NONE or WIDE2-1.
// Make DP_PATH = 0 for NONE, = 1 for a path of WIDE2-1 or enter an altitude (in Meters ASL)
// for a path of WIDE2-1 when the tracker is lower than the entered altitude and for NO PATH
// when higher than that altitude. Switching the path based on the trackers altitude is very
// useful as WIDE2-1 is often needed to reach an I-Gate when on or near the ground, but a
// WIDE2-1 path is very seldom required when higher than 1000 - 2000 meters and should not
// normally be used. (Note: The minimum altitude needed to enable path switching is 100 meters.)
#define DP_PATH  2000 // Enter 0, 1 or an altitude => 100 Meters ASL (Above Sea Level)
// *************************************************

// The following 2 entries provide the WIDE2-1 path when DP_PATH = 1 or an altitude
// => 100 Meters is entered and the tracker is at an altitude lower than that altitude.
// WIDE2-1 is the recommended path and should be used unless familiar with APRS path
// settings and you know the consequences of using something different.
#define DIGI_PATH1      "WIDE2"
#define DIGI_PATH1_TTL    1
// *************************************************


// APRS COMMENT. This is placed in the comment portion of the APRS message. It's best
// to keep this short as the longer the packet, the more vulnerable it is to noise.
#define APRS_COMMENT    "Tracksoar v1.1.2"
// *************************************************


// APRS PERIOD, or Transmit Rate, is how often, in seconds, a transmission will be made.
#define APRS_PERIOD   60    // sec's
// *************************************************

// APRS TIME, or SLOT TIME, is the specific "slot" of time in seconds past the top of the
// minute top of the minute that a transmission will occur when Time Slotted Transmissions 
// are enabled. To enable Time Slotted Transmissions, enter a time (in seconds) or enter -1
// to disable Time Slotted Transmissions.
#define APRS_SLOT      -1    // sec's. (-1 disables slotted transmissions) 
// *************************************************
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

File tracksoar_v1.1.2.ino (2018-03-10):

/* trackuino copyright (C) 2010  EA5HAV Javi

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
   You should have received a copy of the GNU General Public License
   along with this program; if not, write to the Free Software Foundation, Inc.,
   51 Franklin Street, Fifth Floor, Boston, MA  02110-1301, USA.
*/
//**********************************************************************************
// Note: This trackuino software version has been modified for use with a Tracksoar
// Tracker by removing most everything not required for an ATmega328P processor and
// adding code for a number of additional Tracksoar features.
// These changes and additional features were made/supplied by: Barry Sloan, VE6SBS.
// For more info. see ttp://bear.sbszoo.com/construction/traker/Tracksoar/V1-1.htm
//**********************************************************************************
#define VERSION  "Tracksoar v1.1.2\n"

#include "config.h"
#include "afsk_avr.h"
#include "aprs.h"
#include "gps.h"
#include "pin.h"
#include "power.h"
#include "sensors_avr.h"
#include <Arduino.h>
#include <Wire.h>     // Not used here, but needed in this file for other code

#define cbi(sfr, bit) (_SFR_BYTE(sfr) &= ~_BV(bit)) // deactivate internal pull-ups for twi

// For Time Slotted transmissions, the time spent to get_pos(), check_altitude and do an
// aprs_send must be accounted for to have the transmissions occur at the desired slot time
// and BUSY_TIME is the fudge factor used to account for this time which varies a few ms
// each transmission depending on the values involved with the calculations, but not enough
// to not transmit at the correct second. However using DEBUG statements increases the time
// enough that you may see transmission times occur 1 or 2 sec's later than expected and, of
// course, modifying the firmware can also through off the timing so don't forget to check
// that transmission times are correct after making firmware changes and adjust the BUSY_TIME
// as needed to have transmissions accur when they should. 
#define BUSY_TIME  1750    // (ms) A 1300 to 2200 ms duration works for this firmware version.


// Module constants
static const uint32_t VALID_POS_TIMEOUT = 2000;  // ms.

// Module variables
int x = 0;
bool recent_transmission = false;
static int32_t next_aprs = 0;
static int32_t next_alt_check;

void setup()  // ----------------------------------------------------------------------------

// If PTT LED is used as a PTT indicator, turn PTT LED on when power is connected in order to
// confirm tracker is powered until the GPS gets lock and the GPS LED begins to flash.
{ pinMode(PTT_LED_PIN, OUTPUT);
  if (!PTT_LED_AS_PTT)
  { pin_write(PTT_LED_PIN, LOW);
  }
  else
  { pin_write(PTT_LED_PIN, HIGH);
  }

  cbi(PORTC, 4);    // deactivate internal pull-ups for twi
  cbi(PORTC, 5);

  Serial.begin(GPS_BAUDRATE);
  Serial.println();
  Serial.println(VERSION);

  afsk_setup();     // afsk.cpp
  gps_setup();      // gps.cpp
  sensors_setup();  //sensors_avr.cpp

  // If time slotted transmissions enabled, do not start until we get a valid time reference.
  if (APRS_SLOT >= 0)       // -1 disables time slotted transmissions
  { do
    { while (!Serial.available())
        power_save();
    }
    while (!gps_decode(Serial.read()));
    next_aprs = millis() - BUSY_TIME +
                1000 * (APRS_PERIOD - (gps_seconds + APRS_PERIOD - APRS_SLOT) % APRS_PERIOD);
  }
  else    // (if time slotted transmissions disabled)
  { next_aprs = millis();   // make 1st transmission when tracker is powered
  }

  next_alt_check =  next_aprs + 5000;   // 1st_alt_check after each transmission is 5 sec's later.

  if (PTT_LED_AS_PTT)
    pin_write(PTT_LED_PIN, LOW);  // GPS has lock so time to turn OFF the temporary PTT LED power indicator.
}

void get_pos()              // Get a valid position from the GPS
{ int valid_pos = 0;
  uint32_t timeout = millis();
  do
  { if (Serial.available())
      valid_pos = gps_decode(Serial.read());
  }
  while ( (millis() - timeout < VALID_POS_TIMEOUT) && ! valid_pos) ;
}

void led_alarm()            // Visual Alarm Indicator for when there's a problem
{ while (1)                 // Rapidly flash the LED until problem is fixed and power has been cycled
  { pin_write(PTT_LED_PIN, LOW);
    delay(250);
    pin_write(PTT_LED_PIN, HIGH);
    delay(250);
  }
}

void loop()   // MAIN LOOP --------------------------------------------------------------------------
{ if ((int32_t) (millis() - next_aprs) >= 0)    // Time for another APRS frame
  {
#ifdef DEBUG_TIME_SLOT
    Serial.println();
    Serial.println(F("DEBUG_TIME_SLOT, TIME TO BEACON"));
    Debug_Time_Slot();
    Serial.println(F("          get_pos, check_altitude, aprs_send & calculate next_aprs & next_alt_check"));
#endif

    get_pos();
    check_altitude();      // Check Altitude for Peak and Burst
    aprs_send();
    if (APRS_SLOT >= 0)    // If time slotted transmissions enabled
    { next_aprs = millis() - BUSY_TIME +
                  1000 * (APRS_PERIOD - (gps_seconds + APRS_PERIOD - APRS_SLOT) % APRS_PERIOD);
    }
    else    // (if time slotted transmissions disabled)
    { next_aprs += APRS_PERIOD * 1000L;
    }
    recent_transmission = true;
    next_alt_check = next_aprs - (APRS_PERIOD * 1000L) + 5000;       // next_alt_check is 5 sec's after a transmission

#ifdef DEBUG_TIME_SLOT
    Serial.println();
    Serial.print('[');
    Serial.print(millis());
    Serial.print(F("] recent_transmission="));
    Serial.print(recent_transmission);
    Serial.print(F(",  next_alt_check ="));
    Serial.print(next_alt_check);
    Serial.print(F(",  next_aprs = "));
    Serial.println(next_aprs);
#endif

    while (afsk_flush())
    { power_save();
    }
#ifdef DEBUG_MODEM
    afsk_debug();   // Show modem ISR stats from the previous transmission
#endif
  }
  if ((int32_t) (millis() - next_alt_check) >= 0)   // Time to Check for Maximum Altitude and Burst
  {
#ifdef DEBUG_TIME_SLOT
    Serial.println();
    Serial.println(F("DEBUG_TIME_SLOT, TIME TO CHECK FOR MAX ALTITUDE"));
    Debug_Time_Slot();
#endif

    get_pos();
    check_altitude();                               // Check Altitude for Peak and Burst
    finish_checking_altitude();                     // makes prev_alt_ft = alt_ft
    next_alt_check =  next_alt_check + 10000;       // alt_check every 10 sec's
    recent_transmission = false;

#ifdef DEBUG_TIME_SLOT
    Serial.println();
    Serial.println(F("DEBUG_TIME_SLOT - after get_pos, check_altitude, calculating next_alt_check"));
    Debug_Time_Slot();
#endif
  }
  power_save();     // Incoming GPS data or interrupts will wake us up
}
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

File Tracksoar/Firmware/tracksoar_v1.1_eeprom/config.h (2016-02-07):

/* trackuino copyright (C) 2010  EA5HAV Javi
 *
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
 * You should have received a copy of the GNU General Public License
 * along with this program; if not, write to the Free Software
 * Foundation, Inc., 51 Franklin Street, Fifth Floor, Boston, MA  02110-1301, USA.
 */

#ifndef __CONFIG_H__
#define __CONFIG_H__


// --------------------------------------------------------------------------
// THIS IS THE TRACKUINO FIRMWARE CONFIGURATION FILE. YOUR CALLSIGN AND
// OTHER SETTINGS GO HERE.
//
// NOTE: all pins are Arduino based, not the Atmega chip. Mapping:
// http://www.arduino.cc/en/Hacking/PinMapping
// --------------------------------------------------------------------------


// --------------------------------------------------------------------------
// APRS config (aprs.c)
// --------------------------------------------------------------------------

// Set your callsign and SSID here. Common values for the SSID are
// (from http://zlhams.wikidot.com/aprs-ssidguide):
//
// - Balloons:  11
// - Cars:       9
// - Home:       0
// - IGate:      5
#define S_CALLSIGN      "KI6VBK"
#define S_CALLSIGN_ID   11

// Destination callsign: APRS (with SSID=0) is usually okay.
#define D_CALLSIGN      "APRS"
#define D_CALLSIGN_ID   0

// Digipeating paths:
// (read more about digipeating paths here: http://wa8lmf.net/DigiPaths/ )
// The recommended digi path for a balloon is WIDE2-1 or pathless. The default
// is pathless. Uncomment the following two lines for WIDE2-1 path:
#define DIGI_PATH1      "WIDE2"
#define DIGI_PATH1_TTL  1

// APRS comment: this goes in the comment portion of the APRS message. You
// might want to keep this short. The longer the packet, the more vulnerable
// it is to noise. 
#define APRS_COMMENT    "Tracksoar v1 Beta"

// --------------------------------------------------------------------------
// AX.25 config (ax25.cpp)
// --------------------------------------------------------------------------

// TX delay in milliseconds
#define TX_DELAY      300

// --------------------------------------------------------------------------
// Tracker config (trackuino.pde)
// --------------------------------------------------------------------------

// APRS packets are slotted so that multiple trackers can be used without
// them stepping on one another. The transmission times are governed by
// the formula:
//
//         APRS_SLOT (seconds) + n * APRS_PERIOD (seconds)
//
// When launching multiple balloons, use the same APRS_PERIOD in all balloons
// and set APRS_SLOT so that the packets are spaced equally in time.
// Eg. for two balloons and APRS_PERIOD = 60, set APRS_SLOT to 0 and 30, 
// respectively. The first balloon will transmit at 00:00:00, 00:01:00, 
// 00:02:00, etc. and the second balloon will transmit at 00:00:30, 00:01:30,
// 00:02:30, etc.
#define APRS_SLOT     -1     // seconds. -1 disables slotted transmissions
#define APRS_PERIOD   60    // seconds

// GPS baud rate (in bits per second). This is also the baud rate at which
// debug data will be printed out the serial port.
#define GPS_BAUDRATE  9600


// --------------------------------------------------------------------------
// Modem config (afsk.cpp)
// --------------------------------------------------------------------------

// AUDIO_PIN is the audio-out pin. The audio is generated by timer 2 using
// PWM, so the only two options are pins 3 and 11.
// Pin 11 doubles as MOSI, so I suggest using pin 3 for PWM and leave 11 free
// in case you ever want to interface with an SPI device.
#define AUDIO_PIN       3

// Pre-emphasize the 2200 tone by 6 dB. This is actually done by 
// de-emphasizing the 1200 tone by 6 dB and it might greatly improve
// reception at the expense of poorer FM deviation, which translates
// into an overall lower amplitude of the received signal. 1 = yes, 0 = no.
#define PRE_EMPHASIS    1

// --------------------------------------------------------------------------
// Radio config (radio_hx1.cpp)
// --------------------------------------------------------------------------

// This is the PTT pin
#define PTT_PIN           4

// --------------------------------------------------------------------------
// Sensors config (sensors.cpp)
// --------------------------------------------------------------------------
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

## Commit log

2014-11-19 Arduino APRS tracker
    An improved / smaller trackduino clone.
    [trackduino ublox.brd, trackduino ublox.sch]
2014-11-19 reset switch
    added a reset switch and improved RF ground fill.
    [trackduino ublox.brd, trackduino ublox.sch]
2014-11-19 added crystal on atmega 328p
    added a 16mhz crystal to the atmega 328p / arduino. Cleaned up the
    schematic a bit.
    [trackduino1309111914.brd, trackduino1309111914.sch]
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2014-11-19 fixed missing vcc / ground connections
    missed AVCC and AGND
    [trackduino ublox.brd, trackduino ublox.sch]
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2014-11-20 swapped crystal for smaller resonator
    [trackduino1309111914.brd, trackduino1309111914.sch]
2014-11-21 removed level shifters
    removed unnecessary 5v level shifters from boards.
    [trackduino micro.brd, trackduino micro.sch, trackduino nano.brd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]
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2014-11-21 missed a wire
    [trackduino micro.brd]
2014-11-21 fixed some routing
    [trackduino micro.brd]
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2014-11-22 capacitors do not fit underneath things
    [trackduino micro.brd]
2014-11-22 more layout issues
    Test board 1
    [trackduino micro.brd]
2014-11-22 minor fixes
    boards ordered.
    [trackduino micro.sch]
2014-11-22 fixed consistency error on last commit
    [test.brd, trackduino micro.sch]
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2014-11-23 Protoboards Rev 1
    revision 1 prototype boards, these have been sent to osh park for
    manufacture. Parts have been ordered to test these boards.
    [test.brd, trackduino mini.brd, trackduino mini.sch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]
2014-11-24 Revert 658c1f1..8864008
    This rolls back to commit 658c1f11e5b9c3d0ac6cf8412ef3704af54d539a.
    [test.brd, trackduino nano.brd, trackduino nano.sch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]
2014-11-24 Revert 8864008..08ec791
    This rolls back to commit 8864008ccbdc4df3da8dbd79e6a63e8a5caf342f.
    [test.brd, trackduino mini.brd, trackduino mini.sch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]
2014-11-24 Revert "Protoboards Rev 1"
    This reverts commit 8864008ccbdc4df3da8dbd79e6a63e8a5caf342f.
    [test.brd, trackduino nano.brd, trackduino nano.sch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]
2014-11-24 Revert 8864008..532531c
    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
    [test.brd, trackduino mini.brd, trackduino mini.sch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]
2014-11-24 Revert "stuff"
    This reverts commit 658c1f11e5b9c3d0ac6cf8412ef3704af54d539a.
    [trackduino micro.brd]
2014-11-24 Revert 658c1f1..c6afc34
    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
    [test.brd, trackduino micro.brd, trackduino nano.brd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]
2014-11-24 Revert 8864008..40b68b5
    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
    [test.brd, trackduino mini.brd, trackduino mini.sch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]
2014-11-24 Revert 658c1f1..338655d
    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
    [test.brd, trackduino nano.brd, trackduino nano.sch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]
2014-11-24 Revert 8864008..c721b65
    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
    [test.brd, trackduino mini.brd, trackduino mini.sch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]
2014-11-24 Revert "Revert 8864008..c721b65"
    This reverts commit 1e770fae9d4fe301bf64f6128993cadc941d7714.
    [test.brd, trackduino nano.brd, trackduino nano.sch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]
2014-11-24 Revert 8864008..7e8a1de
    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
    [test.brd, trackduino mini.brd, trackduino mini.sch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]
2014-11-25 Revert 3403df9..76b202c
    This rolls back to commit 3403df9037498db32c64046a9108877ce30486f0.
    [test.brd, trackduino micro.brd, trackduino nano.brd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]
2014-11-25 Revert 8864008..d1c2883
    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
    [test.brd, trackduino micro.brd, trackduino mini.brd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]
2014-11-25 Revert 3403df9..f4310d6
    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
    [test.brd, trackduino micro.brd, trackduino nano.brd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]
2014-11-25 Revert 8864008..107cc9b
    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
    [test.brd, trackduino micro.brd, trackduino mini.brd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]
2014-11-25 micro board broken
    The bed file on the micro board was broken, rolled back to a working
    commit and moved it to this good commit.
    [trackduino micro.brd]
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2014-12-03 c530 library fixes
    named pins, cleaned up foot print and added copout
2014-12-04 fixed uc530 library
    fixed pin names / assignments and cleaned up the package a bit.
2014-12-04 added uc530 version
    added a new revision using the uc530 with integrated chip antenna
    [trackduino mini uc530.brd, trackduino mini uc530.sch]
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2014-12-09 minor fixes to smallest boards
    [pico test.brd, pico test.sch, test nano.brd]
2014-12-15 trackuino rev1
    Fixed errors found after assembling the first prototype
    [trackduino mini.brd, trackduino mini.sch]
2014-12-15 updated micro to mk1
    to match the mini
    [trackduino micro.brd, trackduino micro.sch]
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2015-01-12 trackuino micro sensor mk2
    replaced 5v LDO regulator with boost regulator for operation from 2 AA
    or AAA batteries.
    [trackuino micro sensor mk2.brd, trackuino micro sensor mk2.sch]
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2015-01-25 sensor mk2 fixes
    fixed a short on the boost output and serial RX
    [trackuino micro sensor mk2.brd, trackuino micro sensor mk2.sch]
2015-01-25 fixed ground plane bit
    [trackuino micro sensor mk2.brd]
2015-01-25 missing trace
    [trackuino micro sensor mk2.brd]
2015-01-28 DRC check
    ran osh park DRC check and resolved errors.
    [trackuino micro sensor mk2.brd, trackuino micro sensor mk2.sch]
2015-01-28 boost converter fix
    fixed external component placement and added some silkscreen
    [trackuino micro sensor mk2.brd, trackuino micro sensor mk2.sch]
2015-01-28 added part values
    added part values to the schematic.
    [trackuino micro sensor mk2.brd, trackuino micro sensor mk2.sch]
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2015-02-16 replaced inductor
    the 0805 inductor was getting way too hot due to being run well beyond
    saturation. replaced with a 1812 inductor
    [trackuino micro sensor mk2.brd, trackuino micro sensor mk2.sch]
2015-02-17 added output cap
    added a larger value output cap
    [trackuino micro sensor mk2.brd, trackuino micro sensor mk2.sch]
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2015-03-15 replaced sht15
    [trackuino micro sensor mk2.brd, trackuino micro sensor mk2.sch]
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2015-03-16 minor fix
    [trackuino micro sensor mk2.brd]
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2015-03-26 solar replace antenna
    [trackoon solar.brd, trackoon solar.sch]
2015-03-26 solar ground plane fix
    [trackoon solar.brd]
2015-03-26 pdf brds created and chip board shortened
    [trackuino micro sensor chip mk2.brd]
2015-03-27 fixed overlaps on solar
    [trackoon solar.brd]
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2015-03-29 added i2c breakout and fixed ftdi
    added breakouts on all versions for i2c next to the spi header, replaced
    IO breakout headers from .1" to 2mm to accomodate i2c.
    [trackoon solar.brd, trackoon solar.sch, trackuino micro sensor chip mk2.brd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]
2015-03-29 missing i2c trace on chip
    fixed missing i2c trace on the chip board
    [trackuino micro sensor chip mk2.brd, trackuino micro sensor mk2.brd]
2015-03-30 moved via near ublox pin 1
    via near ublox pin 1 is too close for comfort. Moved it slightly
    [trackuino micro sensor chip mk2.brd]
2015-04-05 fixed chip serial GPS connection
    Serial connection between GPS and Avr chip was not wired correctly.
    [trackuino micro sensor chip mk2.brd, trackuino micro sensor chip mk2.sch]
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2015-04-14 Moved all boards to origin
    Moved all the boards such that the lower left most corner is at the
    origin.
    [trackoon solar.brd, trackuino micro sensor chip mk2.brd, trackuino micro sensor mk2.brd]
2015-04-14 lined up 12c / spi headers
    lined up api and i2c headers between the chip, u.fl, and solar versions
    of the board.
    [trackoon solar.brd, trackuino micro sensor mk2.brd]
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2015-04-25 tx rx 2mm headers
    replaced .1” serial headers on chip and non chip version with 2mm
    headers
    [trackuino micro sensor chip mk2.brd, trackuino micro sensor chip mk2.sch, trackuino micro sensor mk2.brd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]
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2015-04-26 Replace sensors with Tracksoar sensors.
    [aprs.cpp]
2015-04-29 Created Mux Test
    Created a new board to see if the MUX will fit in two layers
    [chip mux test.brd, chip mux test.sch]
2015-04-29 Removed Via From Under MCU
    Removed a via from under the ATMEGA328P to prevent any potential
    shorts.
    [trackuino micro sensor chip mk2.brd, trackuino micro sensor mk2.brd]
2015-05-13 4 layer mux board
    removed serial jumpers and replace them with 2 muxes for ease of use.
    [mux chip test mk2.brd, mux chip test mk2.sch]
2015-05-13 added ground planes on inner layers
    added ground planes on inner layers and ran drc.
    [mux chip test mk2.brd]
2015-05-19 Standardized round via
    Changed all via on production boards to round, and moved hidden via on
    solar board out from under the atmega. Also fixed bom to specify
    max-m8q gps.
    [trackoon solar.brd, tracksoar mk2 bom.csv, trackuino micro sensor chip mk2.brd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]
2015-05-19 renamed firmware folder
    renamed the firmware folder since it is no longer in testing.
    [SHT2x.cpp, afsk.cpp, afsk_avr.cpp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]
2015-05-20 moved sda wire on chip
    moved sda wire on chip board to make its path a little cleaner
    [trackuino micro sensor chip mk2.brd]
2015-05-21 removed old mux test
    remove the mux test brd / sch that were unused and unrouted.
    [chip mux test.brd, chip mux test.sch]
2015-05-21 created test folder
    created a test folder for unproven boards and schematics, moved the mux
    test and solar versions to test.
    [mux chip test mk2.brd, mux chip test mk2.sch, trackoon solar.brd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]
2015-05-21 moved test folder to root
    moved the test folder to the habner folder.
    [mux chip test mk2.brd, mux chip test mk2.sch, trackoon solar.brd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]
2015-05-22 resolved DRC errors
    Resolved DRC errors on both versions of the board.
    [trackuino micro sensor chip mk2.brd, trackuino micro sensor mk2.brd]
2015-05-22 Simplified Ground Polygons
    simplified ground polygons and further DRC error resolutions.
    [trackuino micro sensor chip mk2.brd, trackuino micro sensor mk2.brd]
2015-05-26 created shield
    added a standard shield schematic and .brd
    [tracksoar shield.brd, tracksoar shield.sch]
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2015-06-03 Moved mix test LED
    changed the schematic on the mux test to move the pulse per second LED
    to the correct area on the schematic.
    [mux chip test mk2.brd, mux chip test mk2.sch]
2015-06-10 new smaller chip test board
    fiddled with the chip board and shrunk it by .1” in preparation for the
    new 2 meter transmitter.
    [tracksoar slightly smaller chip.brd, tracksoar slightly smaller chip.sch]
2015-06-12 added 2 meter transmitter
    added a test 2 meter transmitter. It is very rough and needs a couple
    of caps after the final amplifier.
    [twometertx.brd, twometertx.sch]
2015-06-21 Removed Reset Switch
    removed reset switch from chip version and added a separate reset line
    for ICSP / FTDI programming
    [trackuino micro sensor chip mk2.brd, trackuino micro sensor chip mk2.sch]
2015-06-21 new shield
    added an updated shield for the chip tracksoar.
    [tracksoar chip shield.brd, tracksoar chip shield.sch]
2015-06-22 Fixed chip shield
    added a cutout to prevent obstructing the GPS chip antenna. Removed an
    extra ground trace form the chip board.
    [tracksoar chip shield.brd, trackuino micro sensor chip mk2.brd]
2015-06-23 created a programming shield
    added a chip shield programming shield
    [tracksoar programmer.brd, tracksoar programmer.sch]
2015-06-23 removed ground traces
    removed unused ground traces on chip board
    [trackuino micro sensor chip mk2.brd]
2015-06-23 ISP 5v short removed
    removed a short from the ISP reset pin to 5v
    [trackuino micro sensor chip mk2.brd]
2015-06-23 2 meter rx fixes
    added ground pours and 4 pin header to the 2 meter rx for a test board.
    [twometertx.brd, twometertx.sch]
2015-06-23 2 meter tx rf amp bias
    added bias circuit to RF amplifier
    [twometertx.brd, twometertx.sch]
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2015-07-09 FTDI Fix
    Rewired micro chip ftdi header so RX / TX were broken out correctly.
    [trackuino micro sensor chip mk2.brd, trackuino micro sensor chip mk2.sch]
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2015-07-30 SHT21.cpp loop fix
    fixed an issue in the SHT21.cpp code that will cause the board to not
    transmit if the SHT21 fails to provide data.
    [SHT2x.cpp]
2015-07-30 added declare of variable starttime
    declared startime variable in SHT21.cpp that prevented the code from
    compiling.
    [SHT2x.cpp]
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2015-08-23 SilkScreen Clean Up and Battery
    Cleaned up silk screen and created a board revision with a GPS backup
    battery
    [trackuino micro sensor chip bat mk2.brd, trackuino micro sensor chip bat mk2.sch]
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2015-08-30 added imbue shield
    added an IMU shield with a 9 dof imu
    [imu shield.brd, imu shield.sch]
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2015-09-15 Shield Updates
    added sd storage shield, added fetid chip to programming shield. Moved
    test boards to correct folder.
    [imu shield.brd, imu shield.sch, sd shield.brd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]
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2015-09-20 replace headers
    replaced 2.54mm headers on all production boards with 2mm headers to
    resolve daughter board issues.
    [Tracksoar v1.brd, Tracksoar v1.sch, imu shield.brd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]
2015-10-02 mirrored sd shield
    flipped components on the sd shield to be on the correct side
    [sd shield.brd]
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2015-10-09 fixed silk screen
    fixed minor errors and overlaps on the silkscreen
    [Tracksoar v1.brd, Tracksoar v1.sch]
2015-10-09 replaced shield
    replace shield with an updated shield template
    [Tracksoar shield.brd, Tracksoar shield.sch, tracksoar chip shield.brd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]
2015-10-09 shield silkscreen fix
    minor fix on shield template silk screen
    [Tracksoar shield.brd, Tracksoar shield.sch]
2015-10-11 Updated Shields
    Re-did all shields to use the new rounded corners and 2mm headers
    [Tracksoar Breakout Shield.brd, Tracksoar Breakout Shield.sch, Tracksoar SD shield.brd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]
2015-10-14 removed old shields
    removed square shields and added values to shield passives
    [Tracksoar SD shield.brd, Tracksoar SD shield.sch, Tracksoar imu shield.brd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]
2015-10-15 removed components below gps
    Removed the step up circuit components below the gps receiver and added
    vias to prevent any interference
    [Tracksoar v1.brd, Tracksoar v1.sch]
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2016-01-24 Fixed shield board length
    fixed the shield length to not interfere with power and radio
    [Tracksoar SD shield.brd, Tracksoar imu shield.brd]
2016-01-24 fixed shield footprint
    [Tracksoar shield.brd]
2016-01-24 replaced sd with eeprom
    the atmega328p does not have enough SRAM to handle the Trackuino duties
    and SD read / write. It has been replace with an ST Micro M24M02 2Mb
    eeprom. This will result in much less RAM usage, a smaller BOM, lower
    cost, and lower power usage. However it also means we lose portability
    of storage and easy computer interfacing. We’ll look at revising this
    in future versions.
    [Tracksoar SD shield.brd, Tracksoar SD shield.sch, Tracksoar imu shield.brd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]
2016-02-04 updates
    added twometertx-micrf300, changed layout of twometertx, changed led
    layout on programmer shield to correct an error, added tracksoar v1.1
    to swap power and ground pins on power input header
    [Tracksoar programmer shield.brd, Tracksoar programmer shield.sch, Tracksoar v1.1.brd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]
2016-02-07 fixed BMP180 pressure sensor output
    fixed an issue with the pressure reported by the BMP180
    [afsk.cpp, afsk_avr.cpp, aprs.cpp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]
2016-05-05 tracksoar v1.2
    Tracksoar v1.2, replaced EOL’d BMP180 and SHT21 sensors with combo
    BME280 sensor. Added an active GPS version of the board for those using
    FPV modules utilizing 1.5GHZ links.
    [Tracksoar v1.2 active gps.brd, Tracksoar v1.2 active gps.sch, Tracksoar v1.2.brd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]
2016-06-01 resolved 1.6.5+ compiling issues
    resolved issues in afsk_avr.cpp / h that prevented the firmware from
    compiling in 1.6.5+
    [Tracksoar SD shield.brd, Tracksoar SD shield.sch, twometertx-micrf300.brd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]
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2016-09-04 Cleaned up the directory structure and fixed old README.
    [Tracksoar Breakout Shield.brd, Tracksoar Breakout Shield.sch, Tracksoar SD shield.brd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]
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2017-04-19 tracksoar v2 rev3
    added GPIO and analog pins to new header with i2c.
    [Tracksoar v2.brd, Tracksoar v2.sch]
2017-04-19 tracksoar v2 rev4
    fixed routing issues on ground, cleaned up schematic to remove overlaps
    and moved items to their proper area of the schematic.
    [Tracksoar v2.brd, Tracksoar v2.sch]
2017-04-24 tracksoar v2 rev5
    added ferrite to 5v output on boost converter. Added 4.7k resistor
    between Vin and AREF to provide battery voltage monitoring.
    [Tracksoar v2.brd, Tracksoar v2.sch]
2017-04-27 Moved Test Boards
    Moved the test boards folder to the hardware repo.
    [Tracksoar v2.brd, Tracksoar v2.sch]
2017-04-29 Updated default i2c address
    changed the default i2c address for the bme280 to the correct 0x76 from
    0x77
2017-06-01 Added Watch Dog Timer
    Added a watchdog timer to prevent locking up during reads of the BME280
    sensor via i2c.
    [tracksoar.ino]

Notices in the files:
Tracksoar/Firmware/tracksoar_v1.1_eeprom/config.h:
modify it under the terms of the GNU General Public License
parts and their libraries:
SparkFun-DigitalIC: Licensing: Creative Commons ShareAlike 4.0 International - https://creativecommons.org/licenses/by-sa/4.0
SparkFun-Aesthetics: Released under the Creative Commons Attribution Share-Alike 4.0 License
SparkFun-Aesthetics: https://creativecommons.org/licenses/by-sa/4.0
